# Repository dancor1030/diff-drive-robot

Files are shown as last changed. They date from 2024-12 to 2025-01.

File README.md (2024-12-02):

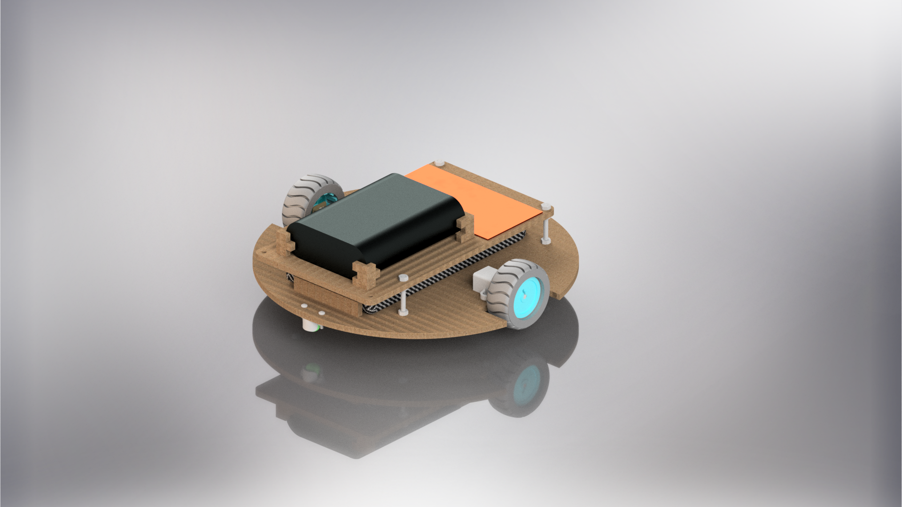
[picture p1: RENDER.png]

# Differential Drive Robot
Differential Drive Robot development for Universidad EIA in Envigado, Antioquia.  Contains all files, including CAD, firmware programming, ROS2 software programming. 

Look at it working in [YouTube](https://youtu.be/ukqRsuS6mHY)

## Authors
- Antonio Cock
- Daniel Correa
- Fernando Velilla
- Raúl Villamil
- Tomás Vélez

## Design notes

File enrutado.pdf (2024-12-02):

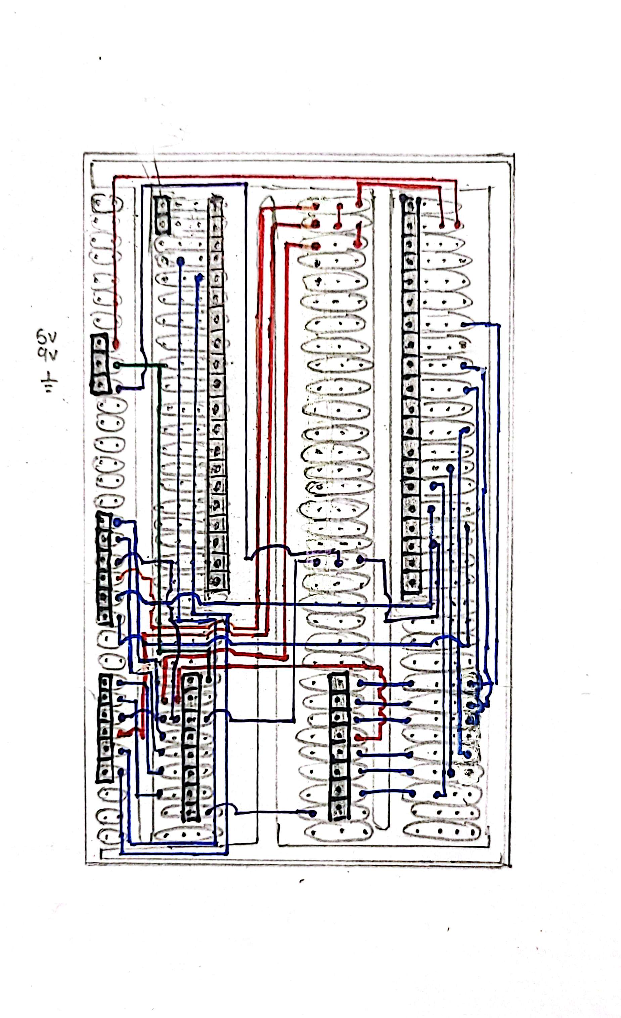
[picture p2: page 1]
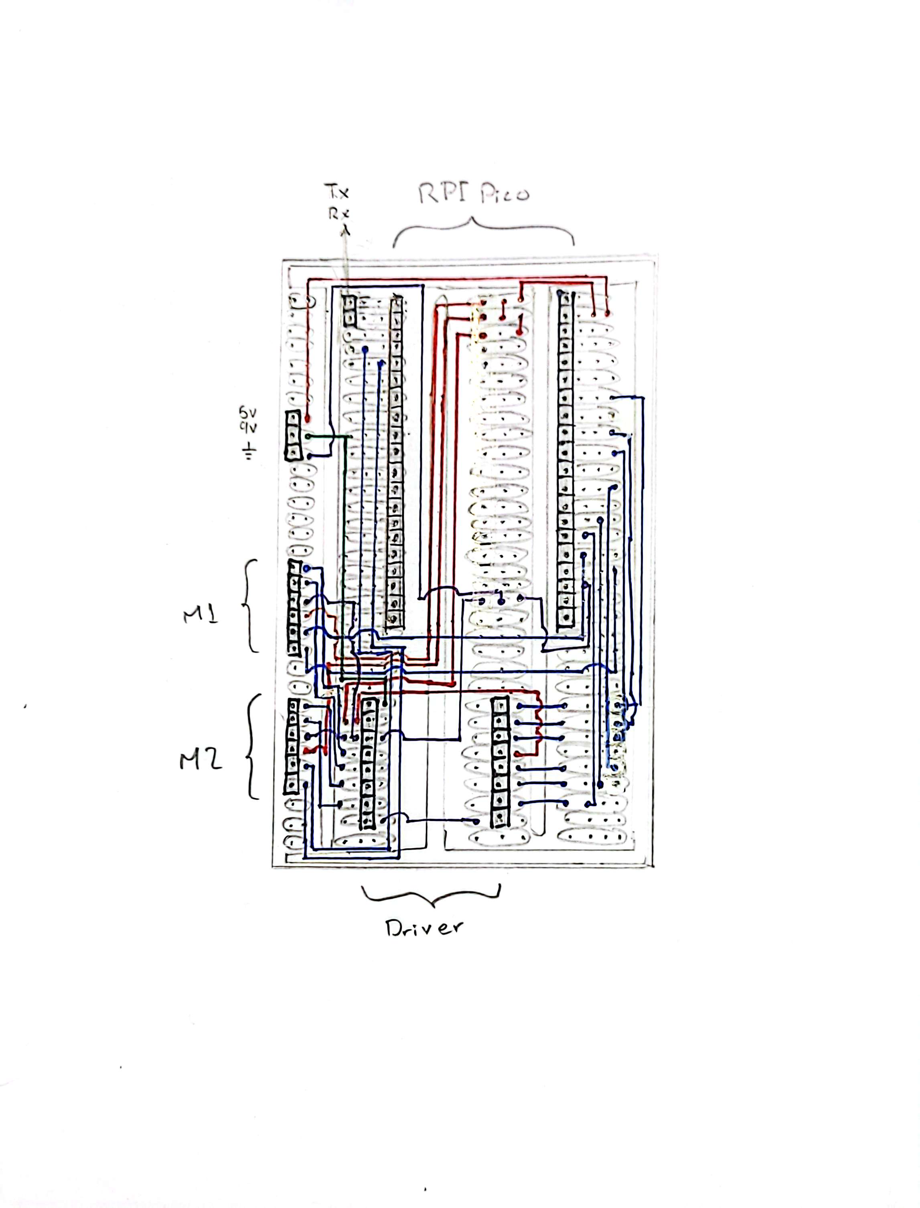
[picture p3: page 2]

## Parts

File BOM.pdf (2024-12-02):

Pololu 1/2 bola metálica | 1 | didacticas electronicas | metal | 9.300 $ | https://www.didacticaselectronicas.com.co/shop/pol-953-rueda-loca-pololu-1-2-bola-metalica-3196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
4 | Separadores | Tornillo M3X30 | 4 | Mundial de tornillos | acero inoxidable | 3.600 $ | https://www.mundialdetornillos.com/
5 | Tuercas M3 | Tuerca M3 | 4 | Mundial de tornillos | acero | 3.200 $ | https://www.mundialdetornillos.com/
6 | Tornillo M2 | Tornillo M2X10 | 6 | Mundial de tornillos | acero inoxidable | 1.200 $
7 | Tuercas M2 | Tuerca M2 | 6 | Mundial de tornillos | acero | 1.000 $
6 | Soporte motor | POL-1089 Soporte para micromotor | 2 | didacticas electronicas | Plastico | 27.300 $
7 | rueda motor | POL-1218 Set rueda 42x19 | 2 | didacticas electronicas | Plastico | 20.000 $
valor final | | | | | | $ 65.600

https://www.mundialdetornillos.com/

https://www.mundialdetornillos.com/

https://www.didacticaselectronicas.com.co/shop/pol-1089-soporte-para-micromotor-blanco-par-1162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

https://www.didacticaselectronicas.com.co/shop/pol-1218-set-rueda-42x19-soporte-y-encoder-1965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

Bill of materials
Elemento | Nombre Pieza | Especificación | Cantidad | Proveedor | Material | Precio | Enlace
1 | Base | - | 1 | Propio | MDF | - $ | -
2 | Placa superior | - | 1 | Propio | MDF | - $ | -
3 | Rueda loca | POL-953 Rueda loca

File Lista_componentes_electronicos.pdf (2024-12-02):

Item | Nombre | referencia | Origen | Proveedor | cantidad | Precio | Enlace
1 | Controlador de motor | TB6612FNG | Suministrado | didacticas
2 | Microcontrolador | Raspberry Pi Pico | Suministrado | didacticas
3 | Micro motor con encoder | GA12-N20 6VDC 200RPM | Suministrado | didacticas
electronicas | 1 | 11.800 $ | https://www.didacticaselectronicas.com.co/shop/tb6612fng-driver-dual-motor-dc-tb6612fng-10322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
electronicas | 1 | 32.750 $ | https://www.didacticaselectronicas.com.co/shop/rpi-pico-h-raspberry-pi-pico-h-21164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
electronicas | 2 | 26.600 $ | https://www.didacticaselectronicas.com.co/shop?search=micro+motor+con+encoder&order=name+asc
4 | Micro computador | Raspberry Pi 4 | Suministrado | SUCONEL | 1 | 370.000 $ | https://suconel.com/productos/raspberry-pi-4-quad-core-64-bit-1gb-wifi-bluetooth-raspberrypi
5 | Bateria | ETHPB8QI 8000mAh | propio | HELIX | 1 | 166.000 $ | https://helixaccessories.com/products/8-000-mah-wireless-power-bank
6 | cables | Cable conexión fácil Dupont H/H 20cm | Suministrado | didacticas
7 | Baquelita de soldadura | Placa de soldadura universal
valor final | | | | | $ 620.222
electronicas | 12 | 3.072 $ | https://www.didacticaselectronicas.com.co/shop/easy-cab-unt-hh-20-cable-conexion-facil-dupont-h-h-20cm-venta-minima-10-unidades-colores-diferentes-16621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
10x7 cm | propio | SUCONEL | 1 | 10.000 $ | https://suconel.com/productos/placa-de-circuito-impreso-universal-11-x-10-cm-suc1011

Lista de componentes electronicos

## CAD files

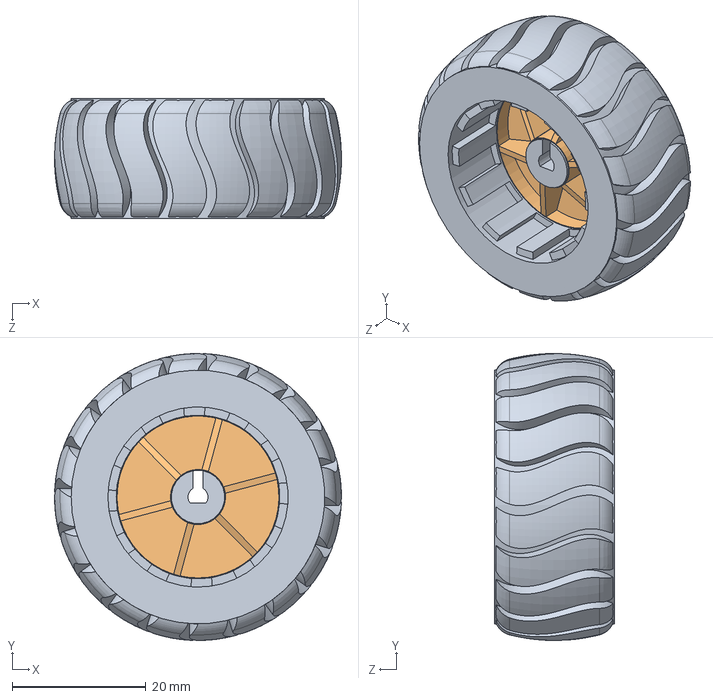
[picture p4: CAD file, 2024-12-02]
CAD/step_cadmodels/RC wheel.SLDASM
43.0 x 43.0 x 18.0 mm
Housing
Hub

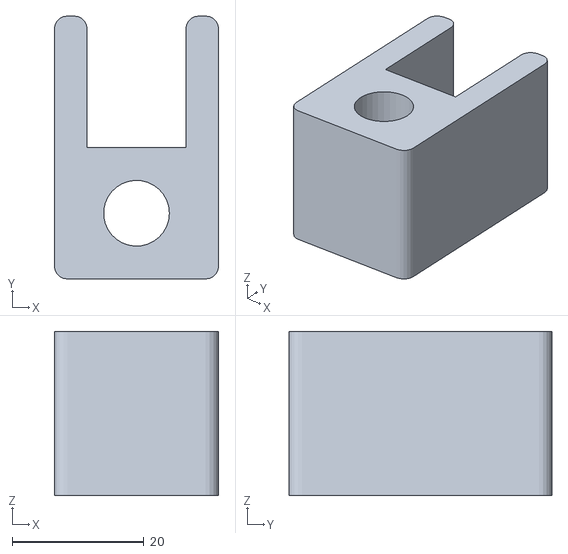
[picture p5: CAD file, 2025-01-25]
code/ros2_ws_2402/install/modelrobot_pkg_gbb/share/modelrobot_pkg_gbb/model/tool_cad.stl
25.0 x 40.0 x 25.0

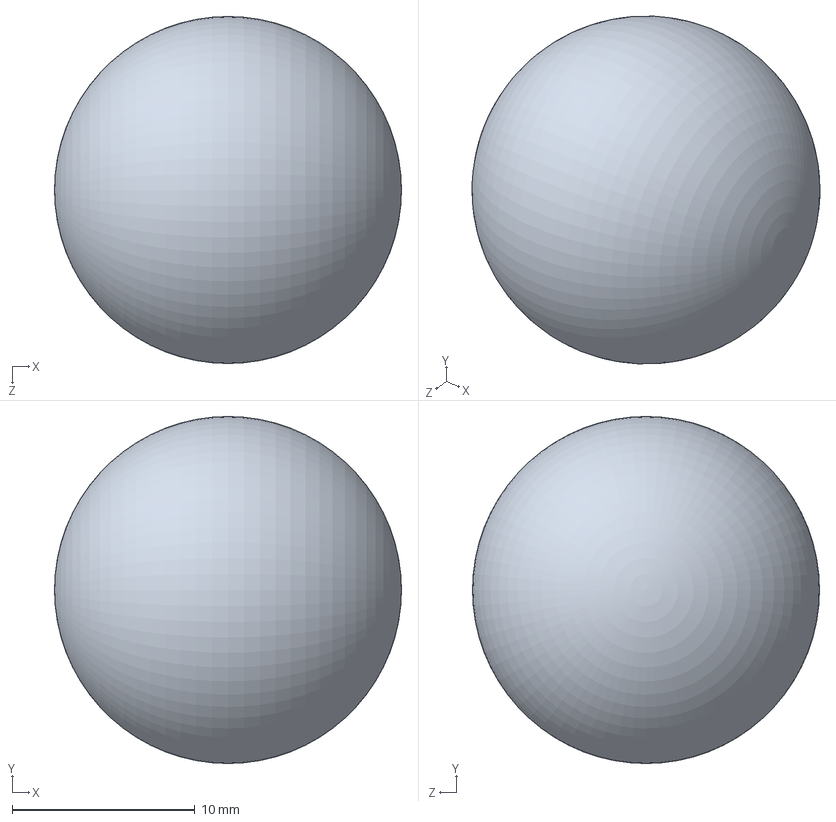
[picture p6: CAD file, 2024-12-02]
CAD/step_cadmodels/balin.SLDPRT
19.0 x 19.0 x 19.0 mm

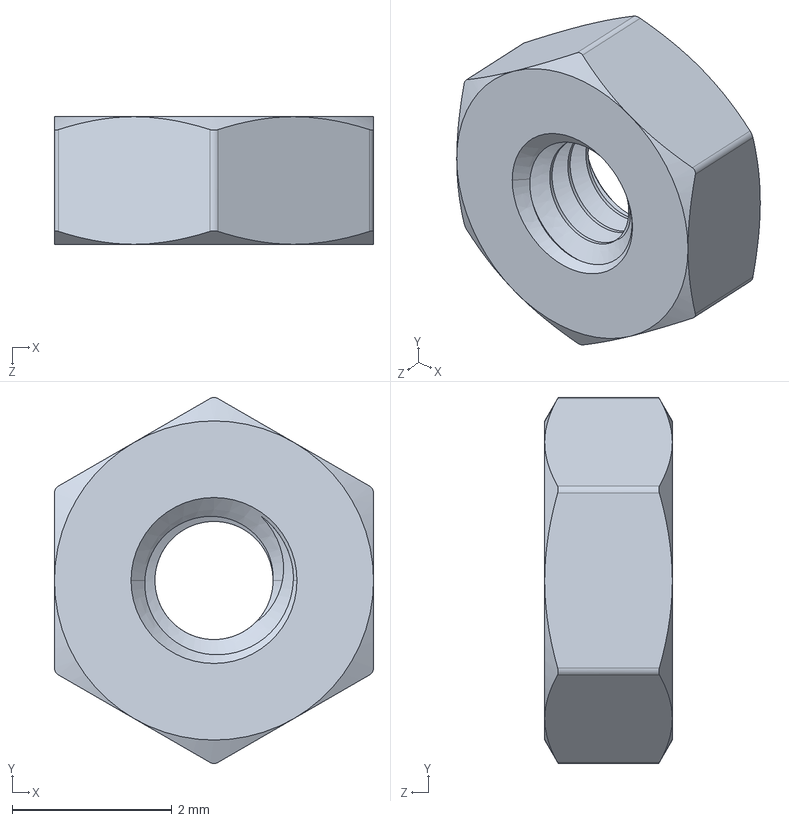
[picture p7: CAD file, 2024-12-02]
CAD/step_cadmodels/nutM2.STEP
4.00 x 4.59 x 1.60 mm

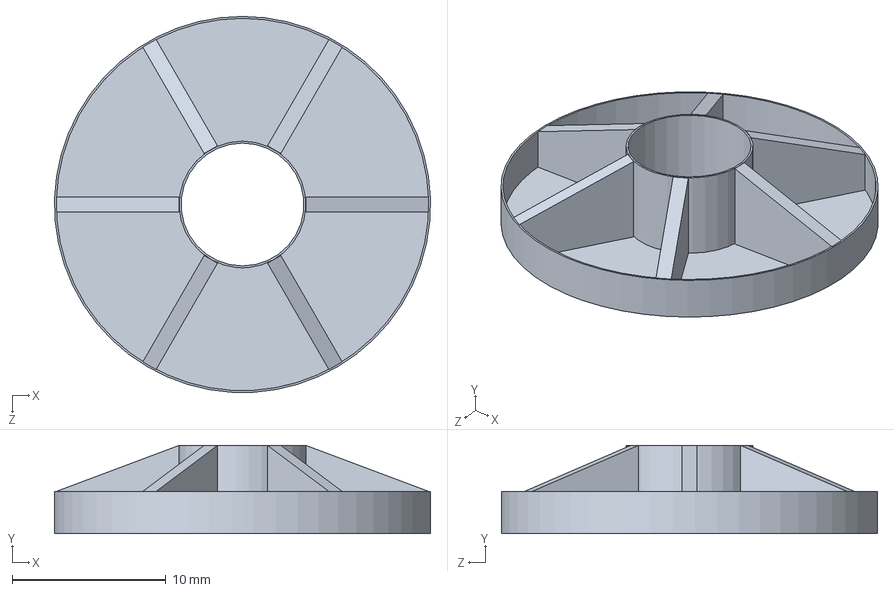
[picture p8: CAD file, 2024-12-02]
CAD/step_cadmodels/Hub.SLDPRT
24.5 x 5.75 x 24.5 mm

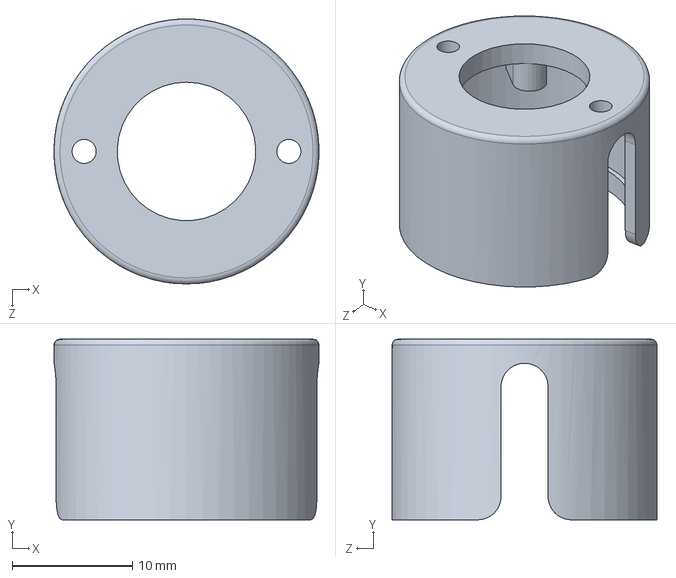
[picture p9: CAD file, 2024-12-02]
CAD/step_cadmodels/CARCASA.SLDPRT
22.0 x 15.0 x 22.0 mm

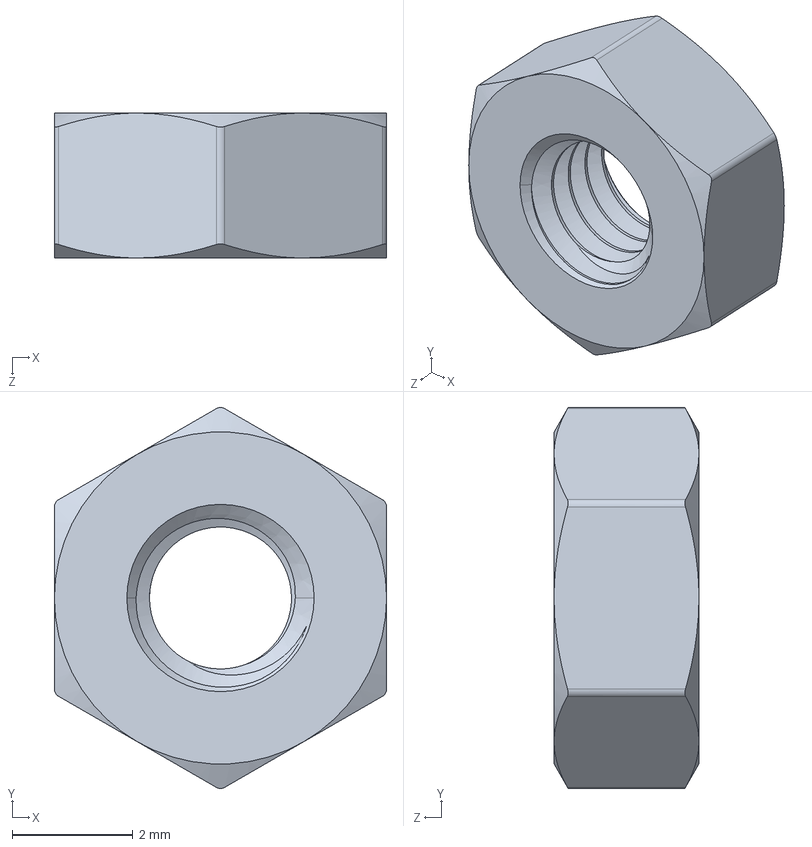
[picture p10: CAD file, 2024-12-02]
CAD/step_cadmodels/nutM3.STEP
5.50 x 6.31 x 2.40 mm

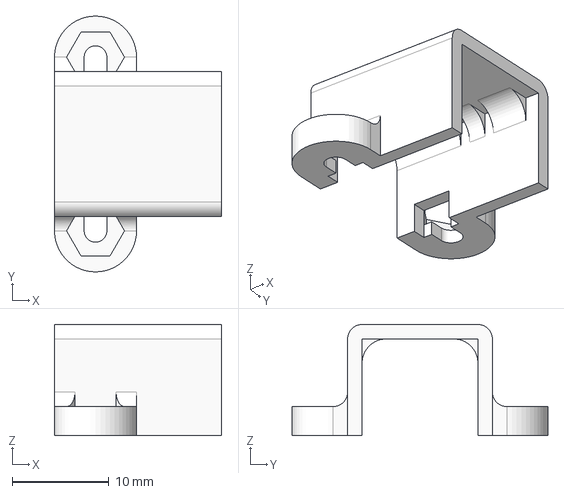
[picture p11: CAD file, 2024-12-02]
CAD/step_cadmodels/N20_Bracket_Extended_Pololu.stp
17.3 x 26.5 x 11.5 mm

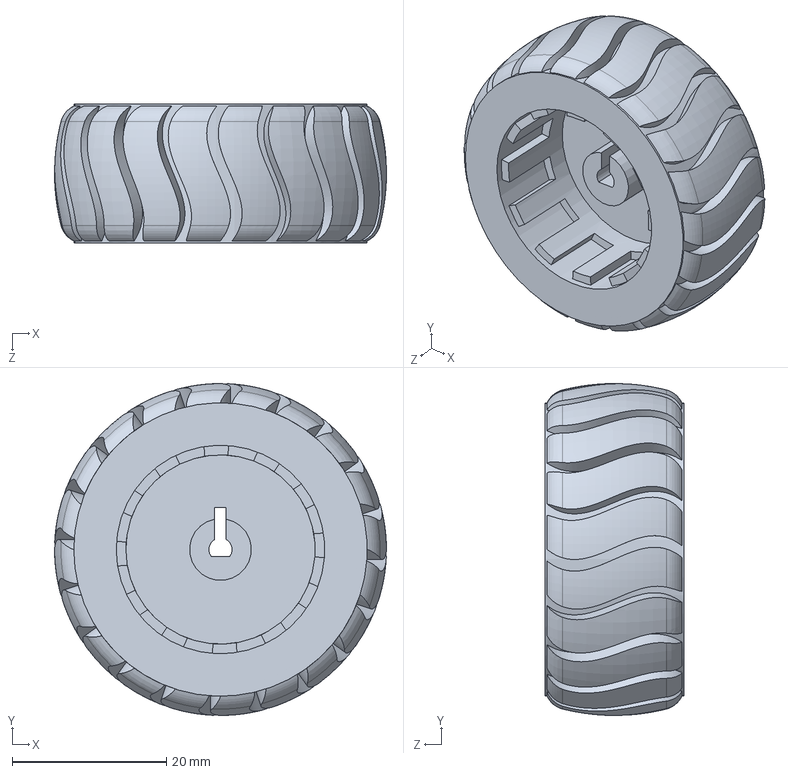
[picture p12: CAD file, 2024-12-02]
CAD/step_cadmodels/Housing.SLDPRT
43.0 x 43.0 x 18.0 mm

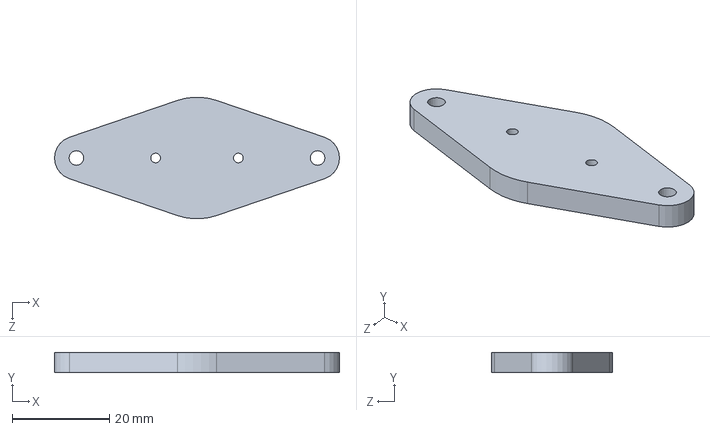
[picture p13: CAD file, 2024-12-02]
CAD/step_cadmodels/base_balin.SLDPRT
58.6 x 4.20 x 24.9 mm

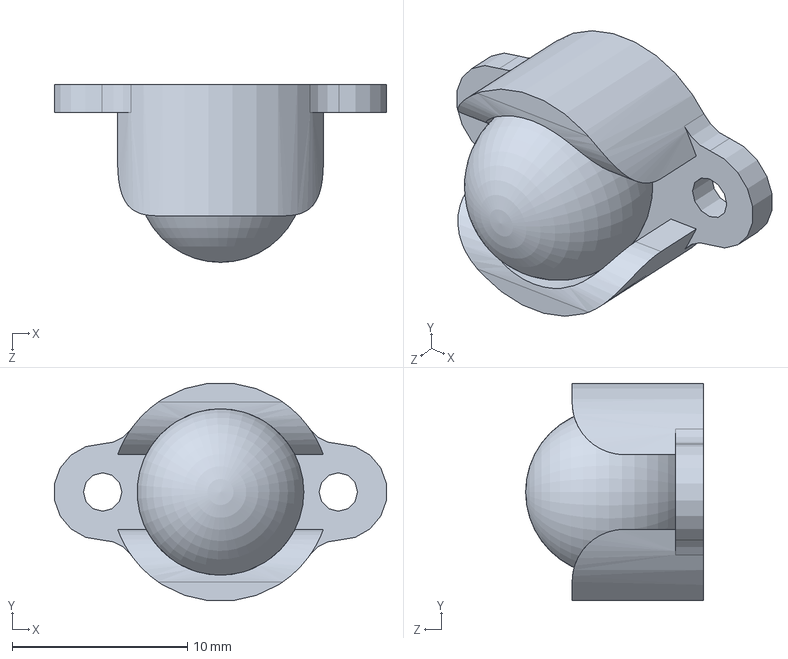
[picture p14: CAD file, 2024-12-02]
CAD/step_cadmodels/caster.SLDPRT
19.0 x 12.4 x 10.2 mm

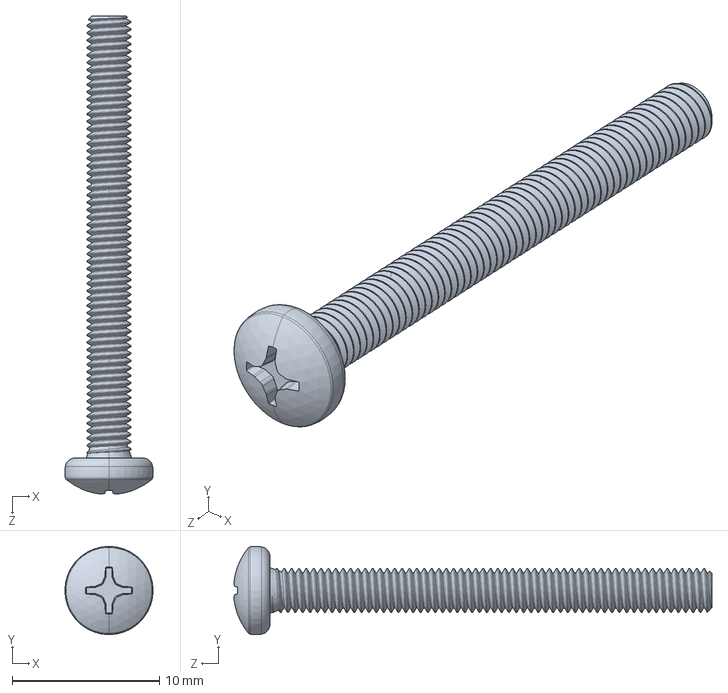
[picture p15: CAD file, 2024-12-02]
CAD/step_cadmodels/screwM3X30.STEP
5.99 x 5.99 x 32.4 mm

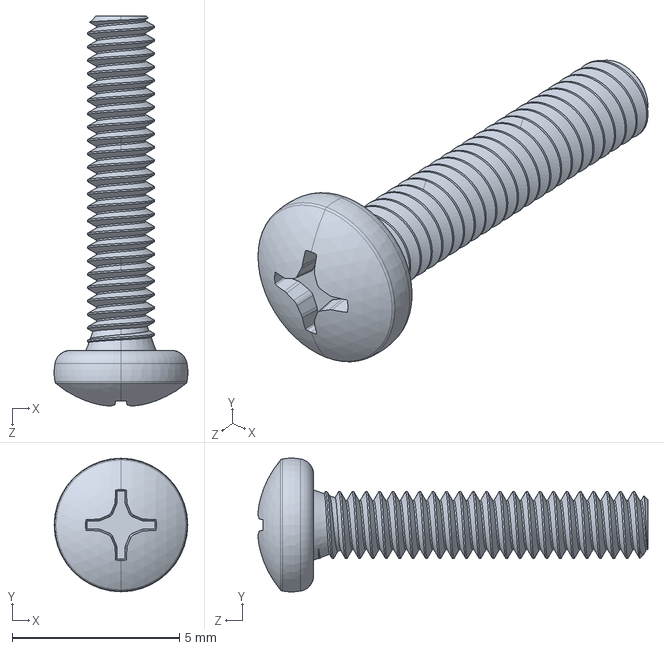
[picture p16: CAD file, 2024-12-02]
CAD/step_cadmodels/screwM2X10.STEP
3.99 x 3.99 x 11.7 mm

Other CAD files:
CAD/ASSEMBLY.iam
CAD/PI4_housing.ipt
CAD/bakelite.ipt
CAD/base.ipt
CAD/corner.iam
CAD/explosionado/OldVersions/explosionado.0002.ipn
CAD/explosionado/explosionado.ipn
CAD/powerbank.ipt
CAD/step_cadmodels/CARCASA/CARCASA.ipt
CAD/step_cadmodels/N20 DC MOTOR/N20 DC MOTOR.ipt
CAD/step_cadmodels/N20_Bracket_Extended_Pololu/N20_Bracket_Extended_Pololu.ipt
CAD/step_cadmodels/N20_Bracket_Extended_Pololu/OldVersions/N20_Bracket_Extended_Pololu.0002.ipt
CAD/step_cadmodels/RC wheel/RC wheel.ipt
CAD/step_cadmodels/balin/balin.ipt
CAD/step_cadmodels/base_balin/base_balin.ipt
CAD/step_cadmodels/caster/OldVersions/caster.0002.ipt
CAD/step_cadmodels/caster/caster.ipt
CAD/step_cadmodels/nutM2/nutM2.ipt
CAD/step_cadmodels/nutM3/nutM3.ipt
CAD/step_cadmodels/screwM2X10/screwM2X10.ipt
CAD/step_cadmodels/screwM3X30/screwM3X30.ipt
CAD/upper_plate.ipt
CAD/wall1.ipt
CAD/wall2.ipt
CAD/wall3.ipt

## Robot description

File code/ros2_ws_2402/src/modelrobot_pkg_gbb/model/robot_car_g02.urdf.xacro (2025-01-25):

<?xml version='1.0'?>
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
<robot xmlns:xacro="http://www.ros.org/wiki/xacro" name="robot_car">
    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
    <xacro:property name="bx" value="${2*100/1000}" /> 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
    <xacro:property name="by" value="${2*80/1000}" />  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
    <xacro:property name="bz" value="${2*50/1000}" />  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
    <xacro:property name="osx" value="${2*25/1000}" /> 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
    <xacro:property name="osy" value="${2*(40+12.5/2)/1000}" /> 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
    <xacro:property name="osz" value="${2*12.5/1000}" /> 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
    <xacro:property name="crad" value="${2*25/1000}" /> 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
    <xacro:property name="clen" value="${2*12.5/1000}" /> 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
    <xacro:property name="caster_rad" value="${2*12.5/1000}" /> 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
    <xacro:property name="caster_osx" value="${2*(100-12.5)/1000}" /> 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
    <xacro:property name="basex" value="${100/1000}" /> 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
    <xacro:property name="basey" value="${100/1000}" /> 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
    <xacro:property name="basez" value="${10/1000}" />   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
    <xacro:property name="blx" value="${25/1000}" />    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
    <xacro:property name="bly" value="${25/1000}" />    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
    <xacro:property name="blz" value="${110/1000}" />   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
    <xacro:property name="bl2z" value="${120/1000}" />  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
    <xacro:property name="half_arm" value="${50/1000}" />       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
    <xacro:property name="joint_axis_dist" value="${100/1000}" /> 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
    <xacro:property name="lateral_offset" value="${25/1000}" />  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
    <xacro:property name="stlscale" value="${1/1000}" />         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
    <xacro:macro name="wheel_macro" params="pname prad plen">
        <link name="${pname}">
            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

            <inertial>
                <mass value="1"/>
                <origin xyz="0 0 0" rpy="0 0 0"/>
                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
            </inertial>

            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
        </link>            
    </xacro:macro>

    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
    <xacro:macro name="arm_link_macro" params="pname parmlen poffset">
        <link name="${pname}">
            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
            <inertial>
                <mass value="1"/>
                <origin xyz="0 0 0" rpy="0 0 0"/>
                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
            </inertial>
            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
        </link>
    </xacro:macro>


    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
    <link name="base_link">
        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
    </link>    

    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
    <link name="base_arm_link">
        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
        <inertial>
            <mass value="1"/>
            <origin xyz="0 0 0" rpy="0 0 0"/>
            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
        </inertial>
        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
    </link>

    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
    <xacro:arm_link_macro pname="boxn1_link" parmlen="${blz}" poffset="${-blz/2}"/>  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    
    <xacro:arm_link_macro pname="boxn2_link" parmlen="${bl2z}" poffset="${-half_arm}"/>   
    <xacro:arm_link_macro pname="boxn3_link" parmlen="${bl2z}" poffset="${-half_arm}"/>   
    <xacro:arm_link_macro pname="boxn4_link" parmlen="${bl2z}" poffset="${-half_arm}"/>  

    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
    <link name="tool_link">
        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
        <inertial>
            <mass value="1"/>
            <origin xyz="0 0 0" rpy="0 0 0"/>
            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
        </inertial>
        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
    </link>

    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
    <joint name="chassis_basearm_joint" type="fixed">
        <parent link="chassis_link"/>
        <child link="base_arm_link"/>
        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
        <origin xyz="${bx/2} 0 ${bz+basez}" rpy="0 0 0"/>
    </joint>                 

    <joint name="basearm_boxn1_joint" type="fixed">
        <parent link="base_arm_link"/>
        <child link="boxn1_link"/>
        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
        <origin xyz="0 0 0" rpy="${-pi/2} 0 0"/>
    </joint>      

    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
    <joint name="boxn1_boxn2_joint" type="revolute">
        <parent link="boxn1_link"/>
        <child link="boxn2_link"/>
        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
        <origin xyz="0 ${-joint_axis_dist} ${-lateral_offset}" rpy="0 0 0"/>
        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
        <axis xyz="0 0 1"/>
        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
        <limit effort="1" lower="${-pi}" upper="${pi}" velocity="1"/>
        <dynamics damping="1" friction="1"/>  
    </joint>    

    <joint name="boxn2_boxn3_joint" type="revolute">
        <parent link="boxn2_link"/>
        <child link="boxn3_link"/>
        <origin xyz="0 ${-joint_axis_dist} ${lateral_offset}" rpy="0 0 0"/>
        <axis xyz="0 0 1"/>
        <limit effort="1" lower="${-pi}" upper="${pi}" velocity="1"/>
        <dynamics damping="1" friction="1"/>  
    </joint>    

    <joint name="boxn3_boxn4_joint" type="revolute">
        <parent link="boxn3_link"/>
        <child link="boxn4_link"/>
        <origin xyz="0 ${-joint_axis_dist} ${-lateral_offset}" rpy="0 0 0"/>
        <axis xyz="0 0 1"/>
        <limit effort="1" lower="${-pi}" upper="${pi}" velocity="1"/>
        <dynamics damping="1" friction="1"/>  
    </joint>    

    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
    <joint name="boxn4_tool_joint" type="revolute">
        <parent link="boxn4_link"/>
        <child link="tool_link"/>
        <origin xyz="0 ${-joint_axis_dist} ${3/2*lateral_offset}" rpy="0 0 ${pi}"/>
        <axis xyz="0 0 1"/>
        <limit effort="1" lower="${-pi}" upper="${pi}" velocity="1"/>
        <dynamics damping="1" friction="1"/>  
    </joint>    

    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
    <joint name="base_chassis_joint" type="fixed">
        <parent link="base_link"/>
        <child link="chassis_link"/>
        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
        <origin xyz="-${osx} 0 -${osz}" rpy="0 0 0"/>
    </joint>

    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
    <link name="chassis_link">
        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

        <inertial>
            <mass value="1"/>
            <origin xyz="0 0 0" rpy="0 0 0"/>
            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
        </inertial>

        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
    </link>    

    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
    <xacro:wheel_macro pname="rwheel_link" prad="${crad}" plen="${clen}"/>
    <xacro:wheel_macro pname="lwheel_link" prad="${crad}" plen="${clen}"/>                       

    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
    <joint name="chassis_rwheel_joint" type="continuous">
        <parent link="chassis_link"/>
        <child link="rwheel_link"/>
        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
        <origin xyz="${osx} ${osy} ${osz}" rpy="0 0 0"/>
        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
        <axis xyz="0 1 0"/>
        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
        <limit effort="1" lower="0" upper="${2*pi}" velocity="1"/>
        <dynamics damping="1" friction="1"/>          
    </joint>    

    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
    <joint name="chassis_lwheel_joint" type="continuous">
        <parent link="chassis_link"/>
        <child link="lwheel_link"/>
        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
        <origin xyz="${osx} -${osy} ${osz}" rpy="0 0 0"/>
        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
        <axis xyz="0 1 0"/>
        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
        <limit effort="1" lower="0" upper="${2*pi}" velocity="1"/>
        <dynamics damping="1" friction="1"/>          
    </joint>        

    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
    <joint name="chassis_caster_joint" type="fixed">
        <parent link="chassis_link"/>
        <child link="caster_link"/>
        <origin xyz="${caster_osx} 0 0" rpy="0 0 0"/>
    </joint>       

    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
    <link name="caster_link">
        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

        <inertial>
            <mass value="1"/>
            <origin xyz="0 0 0" rpy="0 0 0"/>
            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
        </inertial>

        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
    </link>       
</robot>

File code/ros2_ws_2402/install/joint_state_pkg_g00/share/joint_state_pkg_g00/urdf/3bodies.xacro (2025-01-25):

<?xml version='1.0'?>
<robot xmlns:xacro="http://www.ros.org/wiki/xacro" name="robot_car">


    <xacro:property name="blx" value="${0.10/10}" />  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  
    <xacro:property name="bly" value="${0.08/10}" />  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 
    <xacro:property name="blz" value="${0/10}" />   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 
    <xacro:property name="radio" value="${0.9/10}" />   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 
    <xacro:property name="ancho" value="${0.03/10}" /> 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 
   
    <xacro:property name="olx" value="${0.0/10}" />     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 
    <xacro:property name="oly" value="${0.92/10}" />   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 
    <xacro:property name="olz" value="${0.0/10}" />  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 

    <xacro:property name="crad" value="${0.43/2/10}" />  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 
    <xacro:property name="clen" value="${0.09/10}" />  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 
 
    <xacro:property name="srad" value="${0.2/2/10}" />  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 
    <xacro:property name="slx" value="${(1.6/2)/10}" />  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 
    <xacro:property name="slz" value="${(0.08)/10}" />  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

    <xacro:macro name="wheel_macro" params="p_name p_radius p_length">

        <link name="${p_name}">
        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
            <inertial>
            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
                <mass value="1"/>
                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
                <origin xyz="0 0 0" rpy="0 0 0"/>
                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
            </inertial>
            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
        </link>
    </xacro:macro>

  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
    <link name="world">
        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
    </link>

    <joint name="world_worldx_joint" type="prismatic">
        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
        <parent link="world"/>
        <child link="worldx"/>
        <axis xyz="1 0 0"/>
        <origin xyz="0 0 0" rpy="3.14 0 0"/>
        <limit effort="1" lower="-10" upper="10" velocity="10"/>
    </joint>

    <link name="worldx">
        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
    </link>

    <joint name="worldx_worldy_joint" type="prismatic">
        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
        <parent link="worldx"/>
        <child link="worldy"/>
        <axis xyz="0 1 0"/>
        <origin xyz="0 0 0" rpy="0 0 0"/>
        <limit effort="1" lower="-10" upper="10" velocity="10"/>
    </joint>

    <link name="worldy">
        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
    </link>

    <joint name="worldy_worldth_joint" type="continuous">
        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
        <parent link="worldy"/>
        <child link="worldth"/>
        <origin xyz="0 0 0" rpy="0 0 0"/>
        <axis xyz="0 0 1"/>
        <limit effort="1" lower="0" upper="${2*pi}" velocity="10"/>
    </joint>

    <link name="worldth">
        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
    </link>

    <joint name="worldth_base_joint" type="fixed">
        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
        <parent link="worldth"/>
        <child link="base_link"/>
        <origin xyz="0 0 0" rpy="0 3.1415 3.1415"/>
    </joint>

    
    <link name="base_link">
        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
    </link>
    
    <joint name="base_chassis_joint" type="fixed">
        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
        <parent link="base_link"/>
        <child link="chassis_link"/>
        <origin xyz="-${olx} 0 0" rpy="0 0 0"/>
    </joint>

    
    <link name="chassis_link">
        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
        <inertial>
            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
            <mass value="1"/>
            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
            <origin xyz="0 0 0" rpy="0 0 0"/>
            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
        </inertial>
        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
    </link>
    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
    <joint name="chassis_rwheel_joint" type="continuous">
        <parent link="chassis_link"/>
        <child link="rwheel_link"/>
        <origin xyz="${olx} ${oly} ${olz}" rpy="0 0 0"/>
        <axis xyz="0 1 0"/>
        <limit effort="1" lower="0" upper="${2*pi}" velocity="1"/>
        <dynamics damping="1" friction="1"/>  
    </joint>

    <xacro:wheel_macro p_name ="rwheel_link" p_radius ="${crad}" p_length ="${clen}" />
  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
     <joint name="chassis_lwheel_joint" type="continuous">
        <parent link="chassis_link"/>
        <child link="lwheel_link"/>
        <origin xyz="${olx} -${oly} ${olz}" rpy="0 0 0"/>
        <axis xyz="0 1 0"/>
        <limit effort="1" lower="0" upper="${2*pi}" velocity="1"/>
        <dynamics damping="1" friction="1"/>  
    </joint>

    <xacro:wheel_macro p_name ="lwheel_link" p_radius ="${crad}" p_length ="${clen}" />


    <joint name="chassis_caster_joint" type="fixed">
        <parent link="chassis_link"/>
        <child link="caster_link"/>
        <origin xyz="${slx} 0 -${slz}" rpy="0 0 0"/>
        
    </joint>



    <link name="caster_link">
        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
        <inertial>
            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
            <mass value="1"/>
            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n
            <origin xyz="0 0 0" rpy="0 0 0"/>
            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
        </inertial>
        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
    </link>

</robot>

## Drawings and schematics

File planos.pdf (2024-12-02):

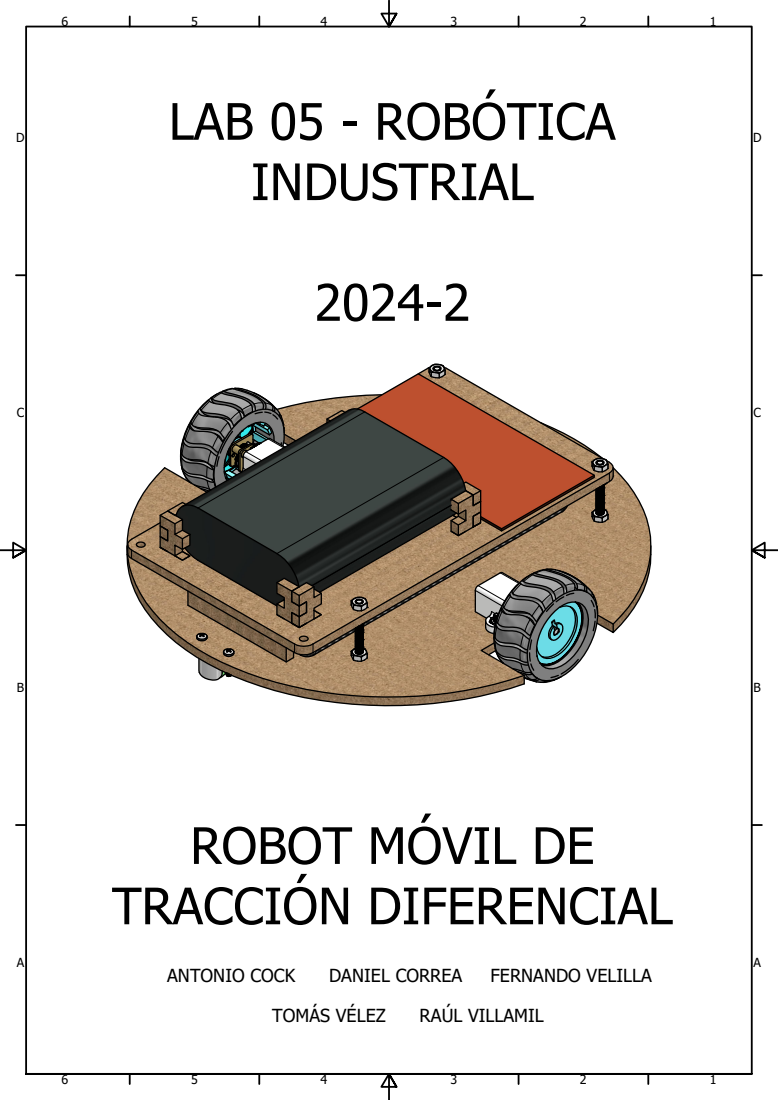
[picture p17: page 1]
LAB 05 - ROBÓTICA; ANTONIO COCK; DANIEL CORREA; FERNANDO VELILLA; TOMÁS VÉLEZ; RAÚL VILLAMIL

ROBOT MÓVIL DE
TRACCIÓN DIFERENCIAL

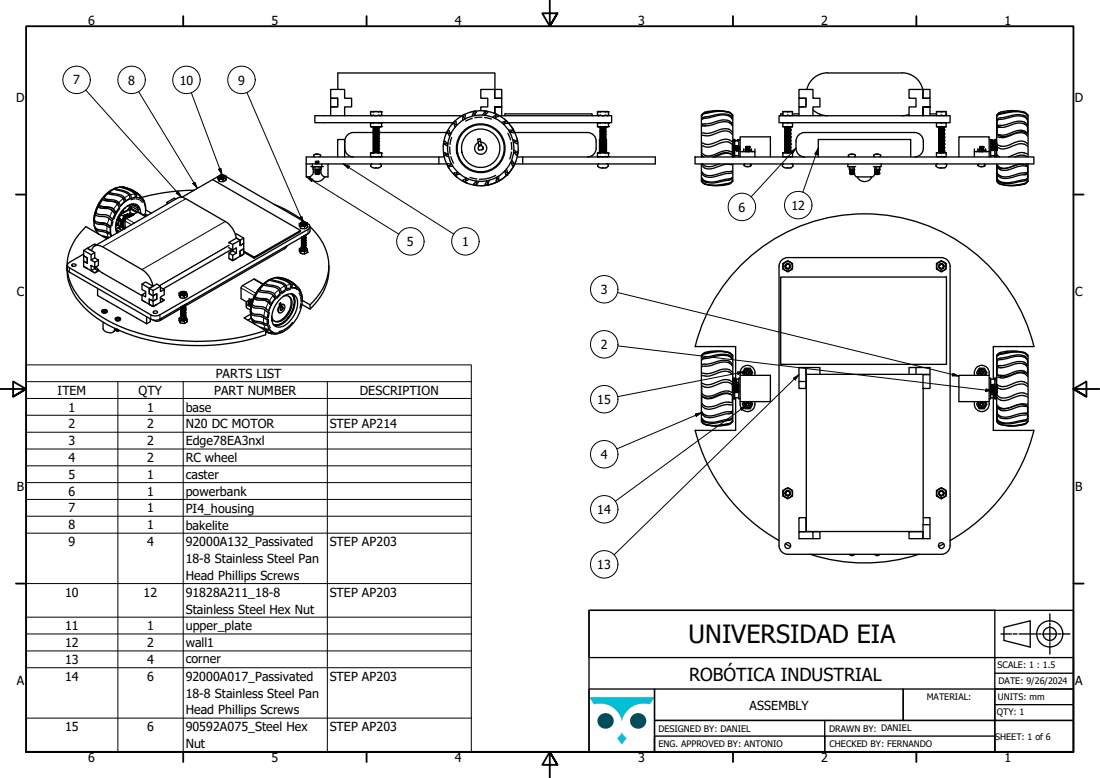
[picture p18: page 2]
PARTS LIST; ITEM; QTY; PART NUMBER; DESCRIPTION; N20 DC MOTOR; STEP AP214; RC wheel; 92000A132_Passivated; STEP AP203; 92000A017_Passivated; 90592A075_Steel Hex; UNIVERSIDAD EIA; ROBÓTICA INDUSTRIAL; SCALE: 1 : 1.5; DATE: 9/26/2024; UNITS: mm; QTY: 1; SHEET: 1 of 6

18-8 Stainless Steel Pan
Head Phillips Screws
Stainless Steel Hex Nut

Nut

DESIGNED BY: DANIEL
ENG. APPROVED BY: ANTONIO

DRAWN BY:
CHECKED BY: FERNANDO

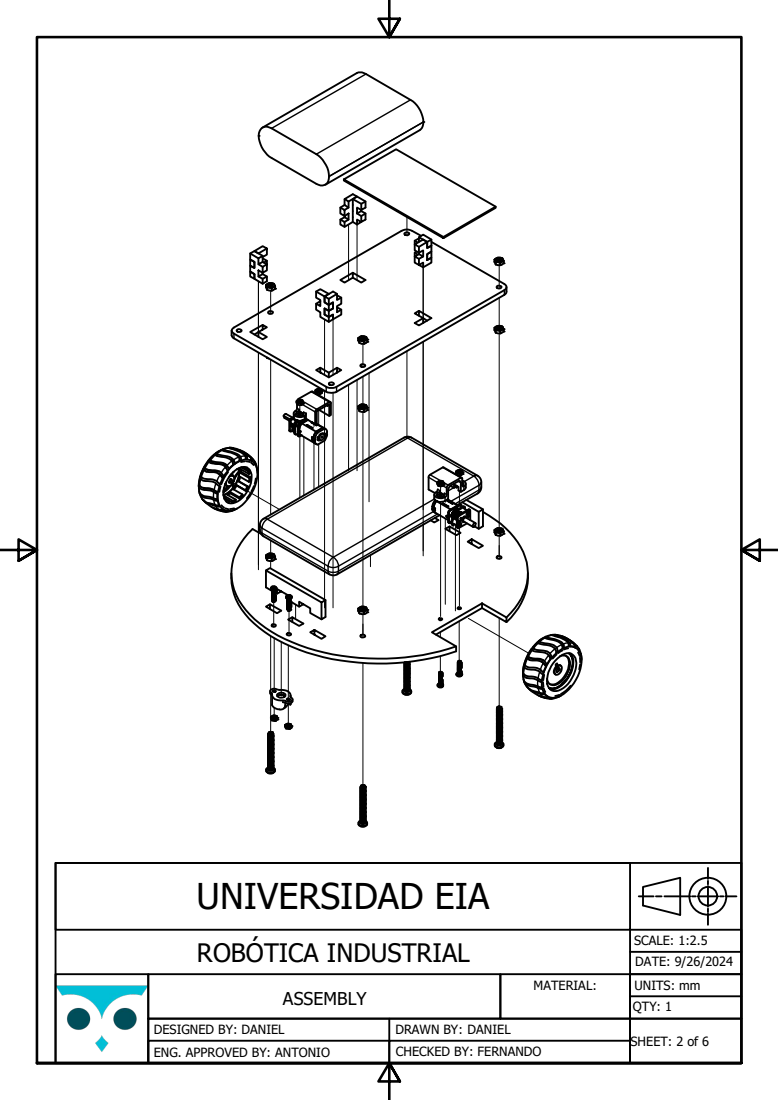
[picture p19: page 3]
DATE: 9/26/2024; UNITS: mm

UNIVERSIDAD EIA

ROBÓTICA INDUSTRIAL | SCALE: 1:2.5

DESIGNED BY: DANIEL | DANIEL

CHECKED BY: FERNANDO

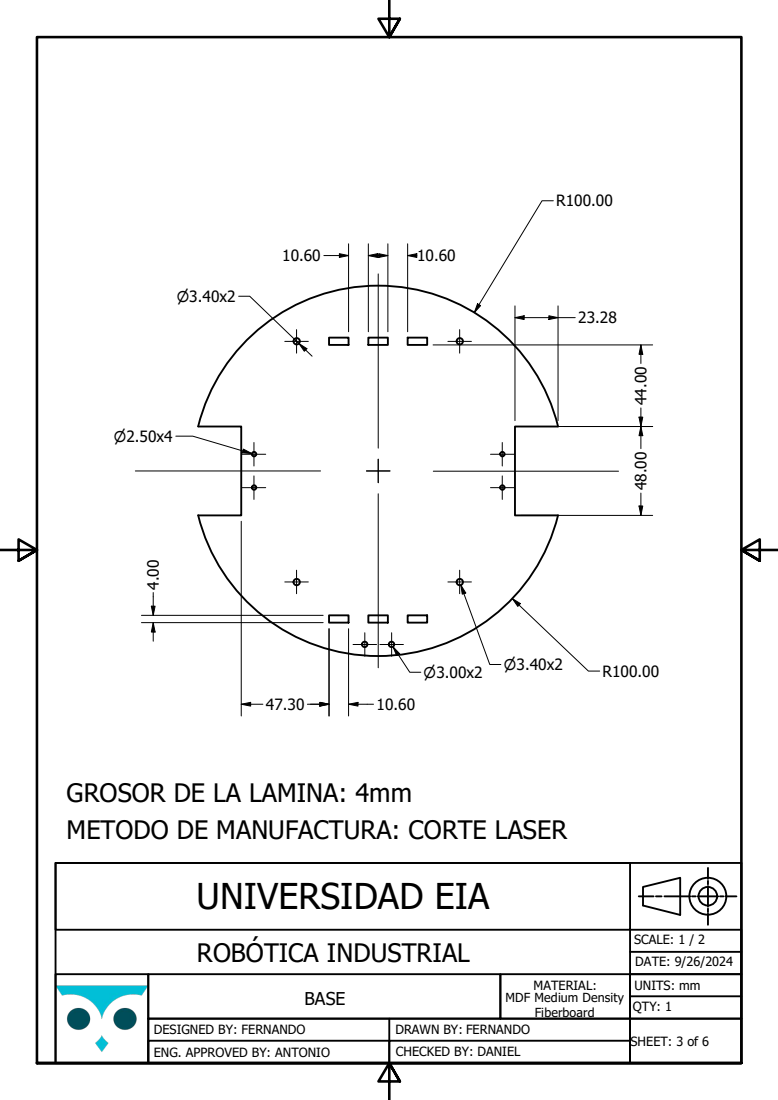
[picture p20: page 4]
DATE: 9/26/2024; UNITS: mm

GROSOR DE LA LAMINA: 4mm
METODO DE MANUFACTURA: CORTE LASER

UNIVERSIDAD EIA

ROBÓTICA INDUSTRIAL | SCALE: 1 / 2

MATERIAL:
MDF Medium Density
Fiberboard

DESIGNED BY: FERNANDO | FERNANDO

CHECKED BY: DANIEL

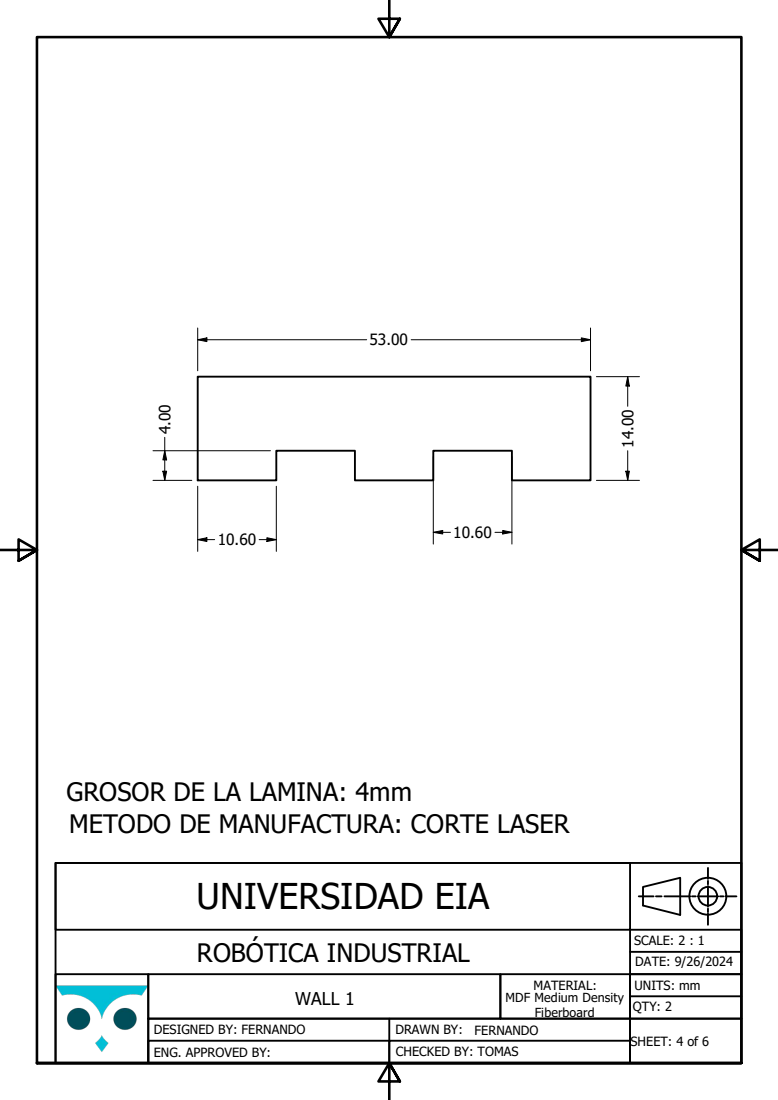
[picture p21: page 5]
DATE: 9/26/2024; UNITS: mm; WALL 1

GROSOR DE LA LAMINA: 4mm
METODO DE MANUFACTURA: CORTE LASER

UNIVERSIDAD EIA

ROBÓTICA INDUSTRIAL | SCALE: 2 : 1

MATERIAL:
MDF Medium Density

DESIGNED BY: FERNANDO | FERNANDO
ENG. APPROVED BY: | CHECKED BY: TOMAS

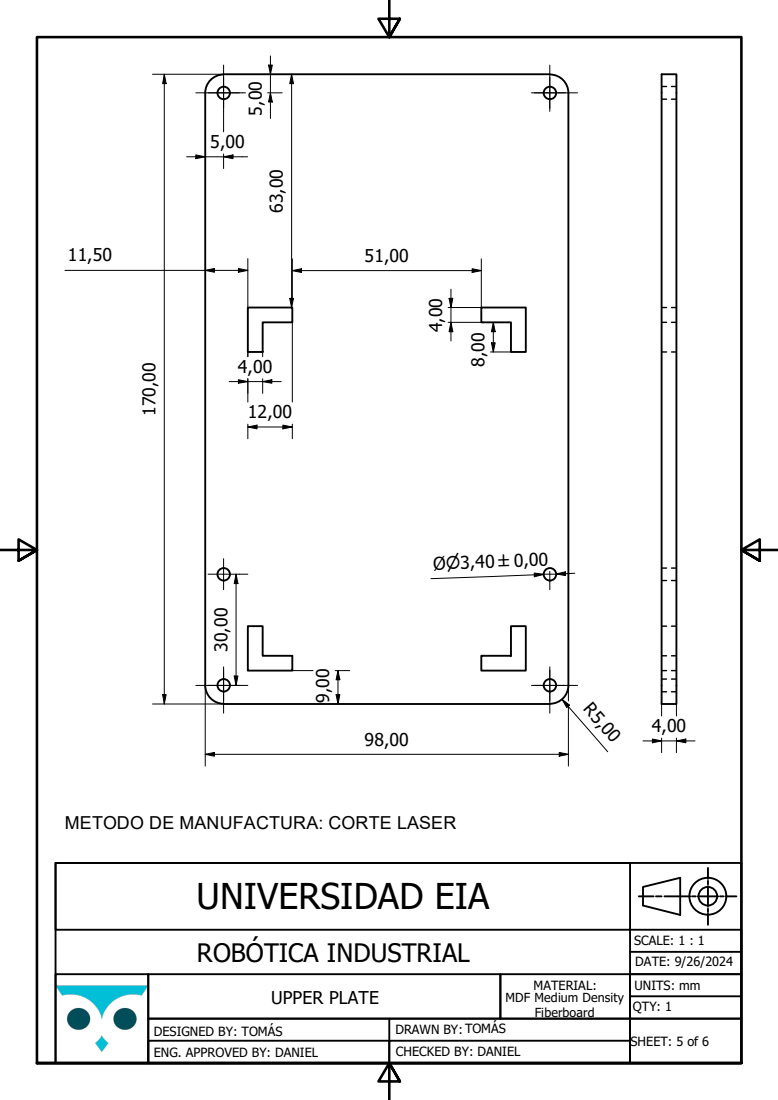
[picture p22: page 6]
DATE: 9/26/2024; UNITS: mm; UPPER PLATE

METODO DE MANUFACTURA: CORTE LASER

UNIVERSIDAD EIA

ROBÓTICA INDUSTRIAL | SCALE: 1 : 1

MATERIAL:
MDF Medium Density

DESIGNED BY: TOMÁS | TOMÁS

ENG. APPROVED BY: DANIEL

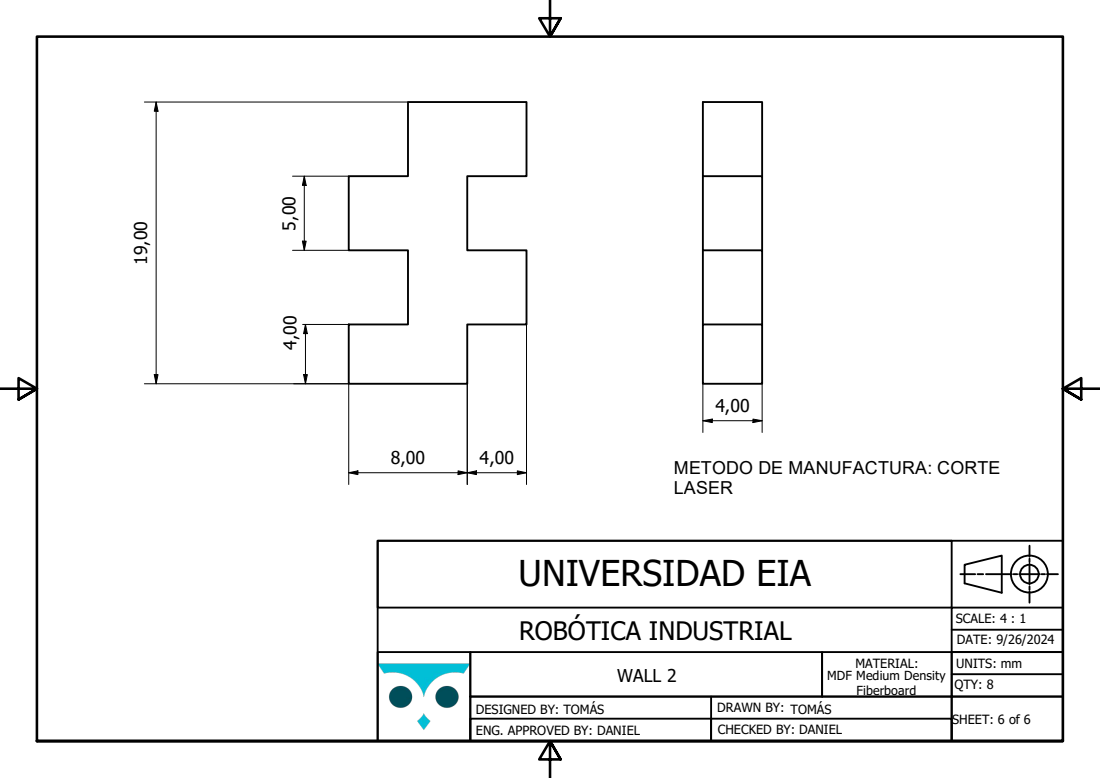
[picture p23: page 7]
DATE: 9/26/2024; UNITS: mm; QTY: 8; WALL 2

METODO DE MANUFACTURA: CORTE
LASER

UNIVERSIDAD EIA

ROBÓTICA INDUSTRIAL | SCALE: 4 : 1

MATERIAL:
MDF Medium Density
Fiberboard

DESIGNED BY: TOMÁS | DRAWN BY: TOMÁS

ENG. APPROVED BY: DANIEL

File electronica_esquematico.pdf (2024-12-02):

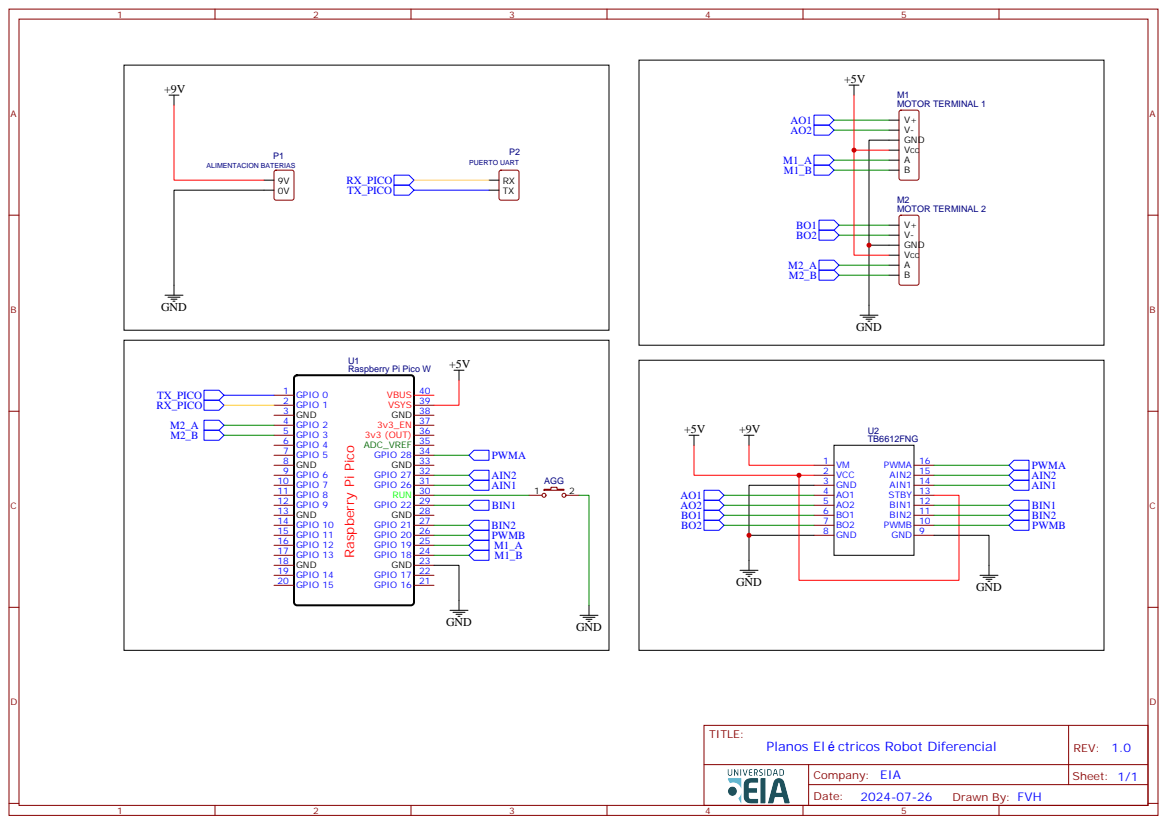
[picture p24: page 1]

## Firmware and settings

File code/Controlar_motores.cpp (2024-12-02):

// main.cpp
#include "Motor.h"
#include "pico_uart_transports.h"

#include <rcl/rcl.h>
#include <rclc/rclc.h>
#include <rclc/executor.h>
#include <geometry_msgs/msg/twist.h>

// Crear dos objetos Motor con los pines
Motor motor1(25, 2, 3, 4, 5, 6, 64, 50.0f);   // Motor 1
Motor motor2(26, 7, 8, 9, 10, 11, 64, 50.0f); // Motor 2

// Variables globales 
float cmd_motor1 = 0.0f;
float cmd_motor2 = 0.0f;

// ROS2 publishers y subscribers
rcl_subscription_t cmd_subs;
geometry_msgs__msg__Twist cmd_msg;

rcl_publisher_t encoder_pub;
geometry_msgs__msg__Twist encoder_msg;

// Funcion mapeo
float map(float x, float in_min, float in_max, float out_min, float out_max) {
    return (x - in_min) * (out_max - out_min) / (in_max - in_min) + out_min;
}

// Callback para el subscriber
void cmd_callback(const void* msgin) {
    const geometry_msgs__msg__Twist* twist_msg = (const geometry_msgs__msg__Twist*)msgin;
    printf("Received commands: linear.x=%f, linear.y=%f\n", twist_msg->linear.x, twist_msg->linear.y);

    // Mapear los comandos a valores de velocidad
    cmd_motor1 = map(twist_msg->linear.x, -3.0f, 3.0f, -100.0f, 100.0f);
    cmd_motor2 = map(twist_msg->linear.y, -3.0f, 3.0f, -100.0f, 100.0f);
}

// Callback para el timer
void timer_callback(rcl_timer_t* timer, int64_t last_call_time) {
    (void)timer;
    (void)last_call_time;

    // Controlar los motores
    motor1.set_motor(cmd_motor1);
    motor2.set_motor(cmd_motor2);

    // Leer las revoluciones de los encoders
    float revs_motor1 = 0.0f;
    float revs_motor2 = 0.0f;
    motor1.calculate_revolutions(&revs_motor1);
    motor2.calculate_revolutions(&revs_motor2);

    // Publicar las posiciones de los encoders
    encoder_msg.linear.x = revs_motor1;
    encoder_msg.linear.y = revs_motor2;

    rcl_publish(&encoder_pub, &encoder_msg, NULL);

    // Alternar LED para indicar actividad
    motor1.toggleLED();
    motor2.toggleLED();
}

int main() {
    // Iniciar comunicacion serial con Micro-ROS
    rmw_uros_set_custom_transport(
        true, NULL,
        pico_serial_transport_open,
        pico_serial_transport_close,
        pico_serial_transport_write,
        pico_serial_transport_read
    );

    // Iniciar ROS 2
    rcl_allocator_t allocator = rcl_get_default_allocator();
    rclc_support_t support;
    rclc_support_init(&support, 0, NULL, &allocator);

    rcl_node_t node;
    rclc_node_init_default(&node, "pico_node", "", &support);

    // Iniciar publisher
    rclc_publisher_init_default(
        &encoder_pub,
        &node,
        ROSIDL_GET_MSG_TYPE_SUPPORT(geometry_msgs, msg, Twist),
        "encoder_topic"
    );

    // Inicializar el subscriber
    rclc_subscription_init_default(
        &cmd_subs,
        &node,
        ROSIDL_GET_MSG_TYPE_SUPPORT(geometry_msgs, msg, Twist),
        "cmd_topic"
    );

    // Inicializar el timer
    rcl_timer_t timer;
    rclc_timer_init_default(
        &timer,
        &support,
        RCL_MS_TO_NS(100),
        timer_callback
    );

    // Inicializar el ejecutor
    rclc_executor_t executor;
    rclc_executor_init(&executor, &support.context, 3, &allocator);
    rclc_executor_add_subscription(&executor, &cmd_subs, &cmd_msg, &cmd_callback, ON_NEW_DATA);
    rclc_executor_add_timer(&executor, &timer);

    // Bucle principal
    while (true) {
        rclc_executor_spin_some(&executor, RCL_MS_TO_NS(100));
    }

    // Limpiar recursos
    rcl_publisher_fini(&encoder_pub, &node);
    rcl_subscription_fini(&cmd_subs, &node);
    rcl_node_fini(&node);

    return 0;
}

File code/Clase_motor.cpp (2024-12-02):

// Motor.h
#ifndef MOTOR_H
#define MOTOR_H

#include <hardware/gpio.h>
#include <hardware/pwm.h>
#include <pico/stdlib.h>
#include <map>

class Motor {
private:
    // Motor driver pins
    const uint LED_PIN;
    const uint ENA_PIN;  // PWM pin for speed control
    const uint IN1_PIN;  // Direction control pin 1
    const uint IN2_PIN;  // Direction control pin 2

    // Encoder pins
    const uint ENCODER_A_PIN;
    const uint ENCODER_B_PIN;

    // Encoder specifications
    const int TICKS_PER_REV;
    const float GR;

    // PWM slice
    uint pwmSlice;

    // Encoder tick counter
    volatile int32_t encoder_ticks;
    int32_t last_ticks;
    static constexpr float time_interval_sec = 0.1f;  // Timer interval in seconds

    // Low-pass filter variables
    static constexpr float alpha = 0.15f;  // Smoothing factor
    float filtered_rpm;

    // Static map to associate encoder pins with Motor instances
    static std::map<uint, Motor*> motor_instances;

    // Private encoder interrupt handler
    static void encoder_irq_handler(uint gpio, uint32_t events);

    // Non-static method to handle the encoder interrupt
    void handle_encoder_interrupt(uint gpio, uint32_t events);

public:
    // Constructor
    Motor(uint led_pin, uint ena_pin, uint in1_pin, uint in2_pin,
          uint enc_a_pin, uint enc_b_pin,
          int ticks_per_rev = 64, float gear_ratio = 50.0f);

    // Motor control functions
    void set_motor(float speed);
    void calculate_revolutions(float* revs);
    void resetEncoderTicks();
    void toggleLED();
};

#endif  // MOTOR_H
// Motor.cpp

#include "Motor.h"

// Initialize the static map
std::map<uint, Motor*> Motor::motor_instances;

Motor::Motor(uint led_pin, uint ena_pin, uint in1_pin, uint in2_pin,
             uint enc_a_pin, uint enc_b_pin,
             int ticks_per_rev, float gear_ratio)
    : LED_PIN(led_pin), ENA_PIN(ena_pin), IN1_PIN(in1_pin), IN2_PIN(in2_pin),
      ENCODER_A_PIN(enc_a_pin), ENCODER_B_PIN(enc_b_pin),
      TICKS_PER_REV(ticks_per_rev), GR(gear_ratio),
      encoder_ticks(0), last_ticks(0), filtered_rpm(0.0f) {
    // Configure GPIO pins for the motor driver
    gpio_init(LED_PIN);
    gpio_set_dir(LED_PIN, GPIO_OUT);
    gpio_put(LED_PIN, 0);  // Turn off LED initially

    gpio_init(IN1_PIN);
    gpio_init(IN2_PIN);
    gpio_set_dir(IN1_PIN, GPIO_OUT);
    gpio_set_dir(IN2_PIN, GPIO_OUT);

    // Set up PWM for speed control on ENA_PIN
    gpio_set_function(ENA_PIN, GPIO_FUNC_PWM);
    pwmSlice = pwm_gpio_to_slice_num(ENA_PIN);
    pwm_set_wrap(pwmSlice, 65535);  // Set PWM wrap for 16-bit resolution
    pwm_set_chan_level(pwmSlice, PWM_CHAN_A, 0);  // Set initial duty cycle (stopped)
    pwm_set_enabled(pwmSlice, true);  // Enable PWM

    // Configure encoder pins and interrupts
    gpio_init(ENCODER_A_PIN);
    gpio_init(ENCODER_B_PIN);
    gpio_set_dir(ENCODER_A_PIN, GPIO_IN);
    gpio_set_dir(ENCODER_B_PIN, GPIO_IN);
    gpio_pull_up(ENCODER_A_PIN);
    gpio_pull_up(ENCODER_B_PIN);

    // Associate encoder pins with this instance
    motor_instances[ENCODER_A_PIN] = this;
    motor_instances[ENCODER_B_PIN] = this;

    // Enable interrupts for encoder pins A and B
    gpio_set_irq_enabled_with_callback(ENCODER_A_PIN,
                                       GPIO_IRQ_EDGE_RISE | GPIO_IRQ_EDGE_FALL,
                                       true, &encoder_irq_handler);
    gpio_set_irq_enabled(ENCODER_B_PIN,
                         GPIO_IRQ_EDGE_RISE | GPIO_IRQ_EDGE_FALL,
                         true, &encoder_irq_handler);
}

void Motor::encoder_irq_handler(uint gpio, uint32_t events) {
    // Find the motor instance associated with this GPIO pin
    Motor* motor = motor_instances[gpio];
    if (motor != nullptr) {
        motor->handle_encoder_interrupt(gpio, events);
    }
}

void Motor::handle_encoder_interrupt(uint gpio, uint32_t events) {
    bool encoder_a = gpio_get(ENCODER_A_PIN);
    bool encoder_b = gpio_get(ENCODER_B_PIN);

    if (gpio == ENCODER_A_PIN) {
        if ((encoder_a && !encoder_b) || (!encoder_a && encoder_b)) {
            encoder_ticks++;  // Forward direction
        } else {
            encoder_ticks--;  // Reverse direction
        }
    } else if (gpio == ENCODER_B_PIN) {
        if ((encoder_a && !encoder_b) || (!encoder_a && encoder_b)) {
            encoder_ticks--;  // Forward direction
        } else {
            encoder_ticks++;  // Reverse direction
        }
    }
}

void Motor::set_motor(float speed) {
    uint16_t pwm_value = static_cast<uint16_t>(fabs(speed));

    if (speed > 0) {
        // Forward direction
        gpio_put(IN1_PIN, 1);
        gpio_put(IN2_PIN, 0);
    } else if (speed < 0) {
        // Reverse direction
        gpio_put(IN1_PIN, 0);
        gpio_put(IN2_PIN, 1);
    } else {
        // Stop the motor
        gpio_put(IN1_PIN, 0);
        gpio_put(IN2_PIN, 0);
    }

    // Set PWM duty cycle for speed control, scaled to 16-bit resolution
    pwm_set_gpio_level(ENA_PIN, (pwm_value * 65535) / 100);  // Map 0-100% to 16-bit PWM
}

void Motor::calculate_revolutions(float* revs) {
    *revs = static_cast<float>(encoder_ticks) / TICKS_PER_REV;
}

void Motor::resetEncoderTicks() {
    encoder_ticks = 0;
    last_ticks = 0;
    filtered_rpm = 0.0f;
}

void Motor::toggleLED() {
    gpio_put(LED_PIN, !gpio_get(LED_PIN));
}
